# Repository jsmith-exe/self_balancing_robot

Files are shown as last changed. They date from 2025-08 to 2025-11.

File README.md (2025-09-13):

## System Architecture

The self-balancing robot is built around a **Rock Pi 4b** and an **ESP32 Dev Module**, which communicate to ensure stable operation and motor control.  

- **Battery & Buck Converter**  
  The LiPo battery supplies power to the system, regulated by a buck converter to safe levels.  

- **Rock Pi 4b**  
  Runs higher-level tasks such as ROS, sensor fusion, and control algorithms.  

- **ESP32 Dev Module**  
  Handles real-time sensor readings from the IMU and encoders, and sends motor commands.  

- **Motor Drivers & Motors**  
  Receive commands from the ESP32 and drive the robot’s wheels.  

- **Sensors**  
  - **9-Axis IMU** provides orientation (yaw, pitch, roll), acceleration, and magnetic heading data.  
  - **Encoders** track wheel rotations for velocity and position feedback.   

Below is the system diagram showing how all the components connect:

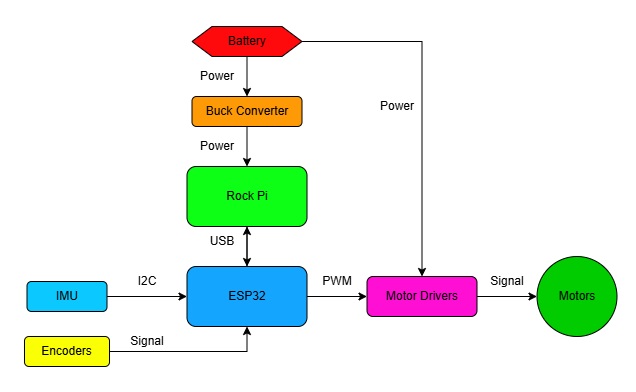
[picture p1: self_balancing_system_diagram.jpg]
System Diagram


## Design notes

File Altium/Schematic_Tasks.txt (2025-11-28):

- Add LEDs for indication of working
- Add buzzer for startup notification
- https://uk.rs-online.com/web/p/compact-power-connectors/1805359

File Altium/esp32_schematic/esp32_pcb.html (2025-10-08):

Altium customize

# Board Information Report

Date: | | 07/10/2025
Time: | | 21:03:08
Elapsed Time: | | 00:00:00
Filename: | | C:\Users\User\self_balancing_robot\Altium\esp32_schematic\esp32_pcb.PcbDoc
Units: | | mmmils

## Contents

Contents

Board Specification

General

## Board Specification

General
Board Size | 84.5mm x 62mm
Components on board | 32

Back to top

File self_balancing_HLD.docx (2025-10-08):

Self-Balancing HLD

Overview

This PCB should be the main connector device between all electronics on the self-balancing robot.

- ESP32 mounted to female header pins
- IMU data in
- USB connectivity between ESP32 and Rock Pi 4b
- Molex PWM output pins for motor driver board

Power

- 12V input from li-ion battery via XT60 connector
- 5V rail from regulator circuitry
- 3V3 rail from ESP32
- Rock Pi 4b powered via USB-C to USB-C from 5V
- ESP32 powered via USB-A to USB-C from Rock Pi 4b

IMU

- MPU-9250 GY-9250 as the IMU
- IMU input to PCB via molex 6 pin connector tied to ESP32 I2C pins
- Powered via 3V3 rail

Motor PWM

- Molex 5 pin output connector tied to ESP32 pins

Motor Inputs from motors

- Molex double row 12 pin motor input connector
- POS and NEG lines of each motor
- 5V, GND, and two encoder lines per motor

Motor Driver Inputs to PCB

- Motor POS and NEG lines will run through a molex 4 pin output connector

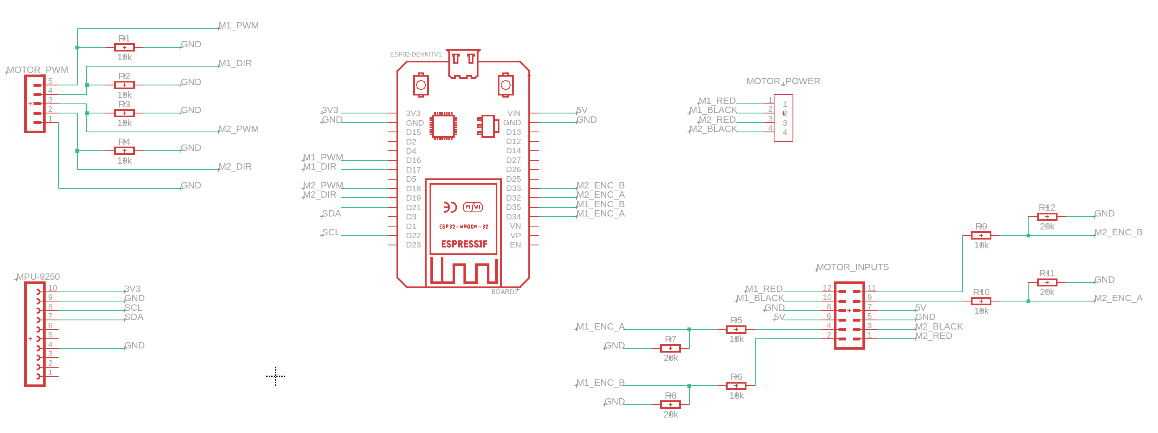
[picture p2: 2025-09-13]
shematics/fusion_schematic.png

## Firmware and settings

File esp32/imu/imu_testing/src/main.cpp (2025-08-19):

#include <Arduino.h>
#include <Preferences.h>
#include "imu_ekf.hpp"

ImuEkf ekf;
Preferences prefs;           // ESP32 NVS (flash) key-value store

float DEFAULT_ROLL_OFFSET = -179.97f;
float DEFAULT_PITCH_OFFSET = -3.34f;

// Persistent mount offsets (degrees) – loaded at boot, applied every run
static float roll_off_deg  = 0.0f;
static float pitch_off_deg = 0.0f;

static float wrap180(float a){
  while (a >  180.0f) a -= 360.0f;
  while (a < -180.0f) a += 360.0f;
  return a;
}

void loadOffsets() {
  prefs.begin("imu", true);       // read-only
  roll_off_deg  = prefs.getFloat("roll_off",  DEFAULT_ROLL_OFFSET);
  pitch_off_deg = prefs.getFloat("pitch_off", DEFAULT_PITCH_OFFSET);
  prefs.end();
}

void saveOffsets(float r_deg, float p_deg) {
  prefs.begin("imu", false);      // read-write
  prefs.putFloat("roll_off",  r_deg);
  prefs.putFloat("pitch_off", p_deg);
  prefs.end();
  roll_off_deg = r_deg;
  pitch_off_deg = p_deg;
}

void setup() {
  Serial.begin(115200);
  delay(200);

  if (!ekf.begin(0x68)) {
    Serial.println("IMU not found at 0x68/0x69");
    while (true) { delay(1000); }
  }

  // Ignore yaw/magnetometer for balancing
  ekf.setTunings(
    1e-3f,   // Q_angle
    1e-5f,   // Q_bias
    2.0f,    // R_rp_deg (roll/pitch noise)
    1000.0f  // R_yaw_deg (huge -> yaw ignored)
  );

  loadOffsets();
  Serial.printf("IMU ready. Using saved offsets: roll_off=%.2f°, pitch_off=%.2f°\n",
                roll_off_deg, pitch_off_deg);
  Serial.println("Commands: 'z' save current R/P as offsets, 'x' clear offsets, 'p' print offsets.");
}

void loop() {
  if (ekf.update()) {
    float r, p, y;
    ekf.getRPY(r, p, y);  // absolute angles vs gravity (deg)

    // Apply persistent mount offsets so “perfectly flat” => 0
    float roll_for_control  = wrap180(r - roll_off_deg);
    float pitch_for_control = wrap180(p - pitch_off_deg);

    // ONE line per sample, nothing else:
    Serial.printf("$RP,%.2f,%.2f\n", roll_for_control, pitch_for_control);
  }

  // Simple serial commands
  if (Serial.available()) {
    int ch = Serial.read();
    if (ch=='z' || ch=='Z') {
      float r, p, y; ekf.getRPY(r, p, y);
      saveOffsets(r, p);
      Serial.printf("Saved new offsets: roll_off=%.2f°, pitch_off=%.2f°\n", r, p);
    } else if (ch=='x' || ch=='X') {
      saveOffsets(0.0f, 0.0f);
      Serial.println("Offsets cleared to 0,0");
    } else if (ch=='p' || ch=='P') {
      Serial.printf("Offsets: roll_off=%.2f°, pitch_off=%.2f°\n", roll_off_deg, pitch_off_deg);
    }
  }
}

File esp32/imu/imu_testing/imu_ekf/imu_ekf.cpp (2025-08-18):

#include "imu_ekf.hpp"
#include <Wire.h>
#include <math.h>
#include <string.h>

// -------- file-scope helpers (avoid scope issues) --------
static inline float deg2rad(float d){ return d * 0.017453292519943295f; }
static inline float rad2deg(float r){ return r * 57.29577951308232f; }
static inline float wrapPI(float a){ while(a >  M_PI) a -= 2*M_PI; while(a < -M_PI) a += 2*M_PI; return a; }
static inline float wrap2PI(float a){ a = fmodf(a, 2*M_PI); if(a < 0) a += 2*M_PI; return a; }

// ===== Public API =====
bool ImuEkf::begin(uint8_t i2c_addr, int sda, int scl, uint32_t i2c_hz){
  addr_ = i2c_addr;
  if (sda >= 0 && scl >= 0) Wire.begin(sda, scl);
  else Wire.begin();                       // ESP32 default SDA=21, SCL=22
  Wire.setClock(i2c_hz);

  // Try 0x68 then 0x69
  if (!imu_.setup(addr_)) {
    addr_ = (addr_ == 0x68) ? 0x69 : 0x68;
    if (!imu_.setup(addr_)) return false;
  }

  // Init covariance
  memset(ekf_.P, 0, sizeof(ekf_.P));
  ekf_.P[0*6+0] = deg2rad(5)*deg2rad(5);
  ekf_.P[1*6+1] = deg2rad(5)*deg2rad(5);
  ekf_.P[2*6+2] = deg2rad(10)*deg2rad(10);
  ekf_.P[3*6+3] = deg2rad(2)*deg2rad(2);
  ekf_.P[4*6+4] = deg2rad(2)*deg2rad(2);
  ekf_.P[5*6+5] = deg2rad(2)*deg2rad(2);

  t_prev_ms_ = millis();
  return true;
}

void ImuEkf::setDeclination(float deg){ decl_deg_ = deg; }
void ImuEkf::setYawOffset(float deg){  yaw_off_deg_ = deg; }

void ImuEkf::setTunings(float Q_angle, float Q_bias, float R_rp_deg, float R_yaw_deg){
  ekf_.Q_angle = Q_angle;
  ekf_.Q_bias  = Q_bias;
  ekf_.R_rp    = deg2rad(R_rp_deg);
  ekf_.R_yaw   = deg2rad(R_yaw_deg);
}

void ImuEkf::seedGyroBias(uint32_t ms){
  Serial.println("GYRO BIAS: keep sensor still...");
  uint32_t t0 = millis(); uint32_t n=0; double sx=0, sy=0, sz=0;
  while (millis() - t0 < ms) {
    if (imu_.update()) { sx+=imu_.getGyroX(); sy+=imu_.getGyroY(); sz+=imu_.getGyroZ(); n++; }
    delay(2);
  }
  float bx=0, by=0, bz=0; if (n>0){ bx=sx/n; by=sy/n; bz=sz/n; }
  ekf_.x[3] = deg2rad(bx);
  ekf_.x[4] = deg2rad(by);
  ekf_.x[5] = deg2rad(bz);
  Serial.printf("Gyro bias [dps]: %+6.3f %+6.3f %+6.3f\n", bx, by, bz);
}

void ImuEkf::calibrateMag(uint32_t ms){
  Serial.println("MAG CAL: rotate in ALL orientations...");
  float minv[3] = { 1e9f, 1e9f, 1e9f }, maxv[3] = { -1e9f, -1e9f, -1e9f };
  uint32_t t0 = millis();
  while (millis() - t0 < ms) {
    if (imu_.update()) {
      float mxx = imu_.getMagX(), myy = imu_.getMagY(), mzz = imu_.getMagZ(); // mG
      if (mxx < minv[0]) minv[0]=mxx; if (myy < minv[1]) minv[1]=myy; if (mzz < minv[2]) minv[2]=mzz;
      if (mxx > maxv[0]) maxv[0]=mxx; if (myy > maxv[1]) maxv[1]=myy; if (mzz > maxv[2]) maxv[2]=mzz;
    }
    delay(10);
  }
  for (int i=0;i<3;i++) mag_.off[i] = 0.5f*(maxv[i]+minv[i]); // mG
  float r[3] = {0.5f*(maxv[0]-minv[0]), 0.5f*(maxv[1]-minv[1]), 0.5f*(maxv[2]-minv[2])};
  float r_avg = (r[0]+r[1]+r[2]) / 3.0f;
  for (int i=0;i<3;i++) mag_.scl[i] = r_avg / (r[i] > 1e-6f ? r[i] : 1.0f);
  mag_.ready = true;

  Serial.printf("MAG CAL done. Offsets (mG): %+6.1f %+6.1f %+6.1f  scales: %.3f %.3f %.3f\n",
                mag_.off[0], mag_.off[1], mag_.off[2],
                mag_.scl[0], mag_.scl[1], mag_.scl[2]);
}

bool ImuEkf::update(){
  if (!imu_.update()) return false;

  // dt
  uint32_t t_now = millis();
  float dt = (t_now - t_prev_ms_) * 0.001f;
  if (dt <= 0) dt = 1.0f/1000.0f;
  t_prev_ms_ = t_now;

  // Read sensors
  float ax = imu_.getAccX(), ay = imu_.getAccY(), az = imu_.getAccZ();        // g
  float gx_dps = imu_.getGyroX(), gy_dps = imu_.getGyroY(), gz_dps = imu_.getGyroZ(); // deg/s
  float mx_mG = imu_.getMagX(),  my_mG = imu_.getMagY(),  mz_mG = imu_.getMagZ();     // mG
  temp_C_ = imu_.getTemperature();

  // Apply mag calibration (mG), then µT
  if (mag_.ready) {
    mx_mG = (mx_mG - mag_.off[0]) * mag_.scl[0];
    my_mG = (my_mG - mag_.off[1]) * mag_.scl[1];
    mz_mG = (mz_mG - mag_.off[2]) * mag_.scl[2];
  }
  float mx_uT = mx_mG * 0.1f, my_uT = my_mG * 0.1f, mz_uT = mz_mG * 0.1f;
  B_uT_ = sqrtf(mx_uT*mx_uT + my_uT*my_uT + mz_uT*mz_uT);

  // Seed angles on first call
  static bool seeded=false;
  if (!seeded) {
    float r,p,y; rpyMeasRad_(ax,ay,az, mx_uT,my_uT,mz_uT, r,p,y);
    ekf_.x[0]=r; ekf_.x[1]=p; ekf_.x[2]=y;
    seeded=true;
  }

  // Inputs u = gyro (rad/s)
  float u[3] = { deg2rad(gx_dps), deg2rad(gy_dps), deg2rad(gz_dps) };

  // Predict + Update
  ekf_.predict(u, dt);
  float z[3]; rpyMeasRad_(ax,ay,az, mx_uT,my_uT,mz_uT, z[0],z[1],z[2]);
  ekf_.update(z);

  // Store outputs (deg)
  roll_deg_  = rad2deg(ekf_.x[0]);
  pitch_deg_ = rad2deg(ekf_.x[1]);
  yaw_deg_   = rad2deg(ekf_.x[2]); if (yaw_deg_ < 0) yaw_deg_ += 360.0f;

  return true;
}

void ImuEkf::getRPY(float &roll_deg, float &pitch_deg, float &yaw_deg) const {
  roll_deg  = roll_deg_;
  pitch_deg = pitch_deg_;
  yaw_deg   = yaw_deg_;
}

// ===== Private helpers =====
void ImuEkf::rpyMeasRad_(float ax, float ay, float az,
                         float mx_uT, float my_uT, float mz_uT,
                         float &roll, float &pitch, float &yaw)
{
  roll  = atan2f(ay, az);
  pitch = -atan2f(ax, sqrtf(ay*ay + az*az));
  float cr = cosf(roll),  sr = sinf(roll);
  float cp = cosf(pitch), sp = sinf(pitch);
  float mxh = mx_uT*cp + mz_uT*sp;
  float myh = mx_uT*sr*sp + my_uT*cr - mz_uT*sr*cp;
  yaw = atan2f(-myh, mxh);
  yaw = wrap2PI(yaw + deg2rad(decl_deg_ + yaw_off_deg_));
}

// ===== EKF internals =====
void ImuEkf::EKF::eye6(float A[36]){ memset(A,0,36*sizeof(float)); for(int i=0;i<6;i++) A[i*6+i]=1; }
void ImuEkf::EKF::add6x6(float C[36], const float A[36], const float B[36]){ for(int i=0;i<36;i++) C[i]=A[i]+B[i]; }
void ImuEkf::EKF::mult6x6(float C[36], const float A[36], const float B[36]){
  for(int i=0;i<6;i++) for(int j=0;j<6;j++){
    float s=0; for(int k=0;k<6;k++) s+=A[i*6+k]*B[k*6+j]; C[i*6+j]=s;
  }
}
void ImuEkf::EKF::mult6x6T(float C[36], const float A[36], const float BT[36]){
  for(int i=0;i<6;i++) for(int j=0;j<6;j++){
    float s=0; for(int k=0;k<6;k++) s+=A[i*6+k]*BT[j*6+k]; C[i*6+j]=s;
  }
}
void ImuEkf::EKF::mult3x6(float C[18], const float A[18], const float B[36]){
  for(int i=0;i<3;i++) for(int j=0;j<6;j++){
    float s=0; for(int k=0;k<6;k++) s+=A[i*6+k]*B[k*6+j]; C[i*6+j]=s;
  }
}
void ImuEkf::EKF::mult6x3(float C[18], const float A[36], const float B[18]){
  for(int i=0;i<6;i++) for(int j=0;j<3;j++){
    float s=0; for(int k=0;k<6;k++) s+=A[i*6+k]*B[k*3+j]; C[i*3+j]=s;
  }
}
void ImuEkf::EKF::mult3x6_6x3(float C[9], const float A[18], const float B[18]){
  for(int i=0;i<3;i++) for(int j=0;j<3;j++){
    float s=0; for(int k=0;k<6;k++) s+=A[i*6+k]*B[k*3+j]; C[i*3+j]=s;
  }
}
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

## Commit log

2025-08-18 imu zeroed
2025-08-19 ros node for imu on rock
2025-08-19 imu ouptut RP
2025-09-13 fusion schematic
2025-10-08 updated schematic
    [esp32.SchDoc, esp32_schematic.PrjPcb]
2025-10-08 connector changes
    [esp32.SchDoc]
2025-10-09 terminal block added
    [esp32.SchDoc]
2025-10-10 tidy up encoder pins
    [esp32.SchDoc]
2025-10-10 moving components about
    [esp32.SchDoc]
2025-10-10 bulk caps added
    [esp32.SchDoc]
2025-10-12 dimensions added
    [Indication.SchDoc, esp32.SchDoc]
2025-10-15 switch v1
    [esp32.SchDoc, power_on.SchDoc]
2025-10-21 leds added
    [esp32_schematic.PrjPcb, power_on.SchDoc]
2025-11-04 +5 regulation
    [esp32.SchDoc, power_on.SchDoc]
2025-11-11 andor work day
    [7794.SchLib, KEYSTONE_7794.PcbLib, esp32.SchDoc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]
2025-11-11 lots of board layout done
    [esp32.SchDoc, power_on.SchDoc]
2025-11-11 only divider resistors left
    [esp32.SchDoc, power_on.SchDoc]
2025-11-12 esp pwr added
    [esp32.SchDoc, power_on.SchDoc]
2025-11-12 power switch sorted
    [esp32.SchDoc, power_on.SchDoc]
2025-11-28 gnds connected, encoder level shifter
    [esp32.SchDoc, power_on.SchDoc]
2025-12-11 new regulator in , gnds all tied
    [esp32.SchDoc, power_on.SchDoc]
2025-12-30 voltage reg & level shifter sorted
    [esp32.SchDoc, esp32_schematic.PrjPcb, headers.SchDoc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]
2025-12-30 sheets organised and ports added
    [esp32_schematic.PrjPcb, headers.SchDoc, main_logic.SchDoc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]
2025-12-30 IMU header now 7 pin to allow for INT connection
    [headers.SchDoc, microcontroller.SchDoc]
2026-02-12 colour added
    [main.SchDoc]
2026-06-23 schematic refresh
    [Encoders.SchDoc, IMU.SchDoc, Newton_Alpha.PrjPcb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]
2026-06-23 updated high level sch
    [Encoders.SchDoc, IMU.SchDoc, Level_Shifter.SchDoc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]
